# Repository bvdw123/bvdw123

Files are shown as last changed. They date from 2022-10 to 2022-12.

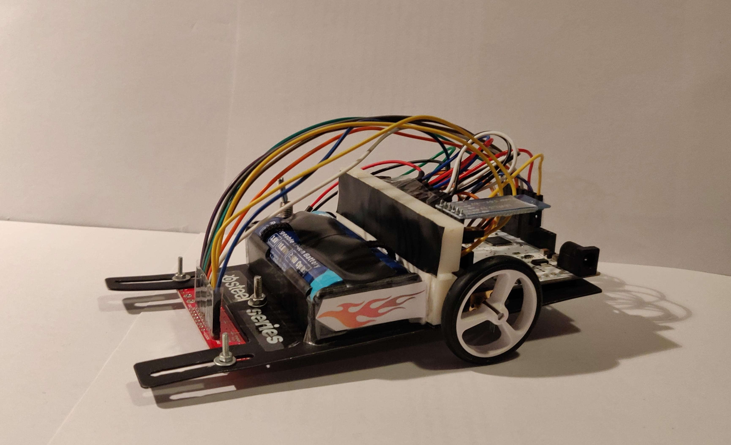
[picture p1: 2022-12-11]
technische tekeningen/mechanisch/LineFollower.jpg

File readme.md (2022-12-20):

# LineFollower
<br />
<br />
<br />
LineFollower

<br />
<br />
  
## specifications
<br />
microcontroller: Arduino Leonardo
<br />
motors: Micro Metal Gearmotor 50:1 
<br />
h-bridge: DRV8833
<br />
sensors: QTR-8A
<br />
batteries: XTAR 18650 Li-Ion
<br />
wireless communication: HC-05
<br />
distance sensor - motors: 85 mm
<br />
weight: 240 g
<br />
speed: 0,431 m/s
<br />

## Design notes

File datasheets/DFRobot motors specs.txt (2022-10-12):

 Specification 50:1

    Motor speed (No gearbox):13000 rpm
    Gear ratio: 50:1 
    Motor speed (with gearbox): 400rpm±10%
    Rated current: 55mA @ 6V
    Stall current: 350mA @ 6V
    Stall torque: 0.39kg*cm @ 6V

 Specification 30:1

    Working voltage: 3 or 6 volts
    15000 rpm @6v No load
    30:1 Gear ratio
    700rpm±10% @6V With load
    No-load Current: 55mA @ 6V
    700mA stall current @ 6V
    Torque:1.2Kg/cm @6V

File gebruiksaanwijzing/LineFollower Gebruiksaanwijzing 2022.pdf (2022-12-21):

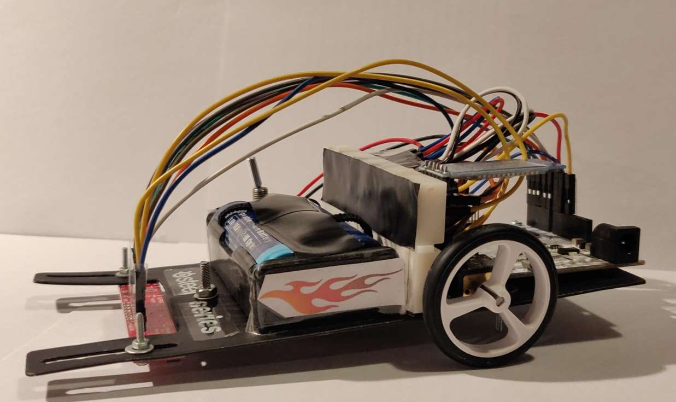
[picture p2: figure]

1
Handleiding $teelseries Ultra Speed Max Performance LineFollower

# Gebruiksaanwijzing $teelseries Ultra Speed Max Performance LineFollower

Benjamin Vande Walle | 3 EM-AM 2022

In dit document wordt beschreven hoe de $teelseries Ultra Speed Max Performance LineFollower veilig te gebruiken.

2

## Inhoud

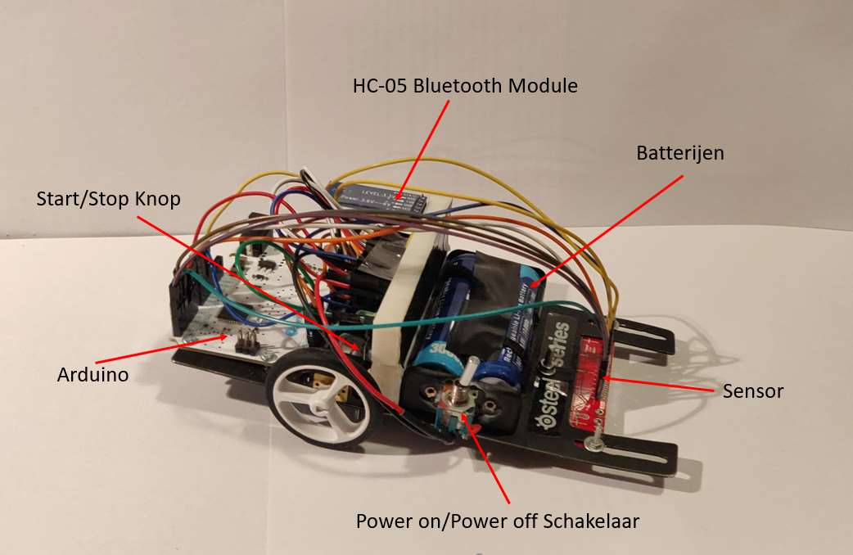
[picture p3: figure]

3

## 1 Algemene waarschuwing

Vrijwaring: bevat kleine onderdelen die een mogelijks verstikkingsgevaar vormen, niet geschikt voor kinderen onder 12 jaar, altijd onder ouderlijk toezicht gebruiken.
Bij verkeerd gebruik van de $teelseries Ultra Speed Max Performance LineFollower gevaar op rook-en vuurontwikkeling. De ontwerper van de $teelseries Ultra Speed Max Performance LineFollower is niet verantwoordelijk voor enige vorm van schade zowel lichamelijk als materieel.

## 2 Overzicht LineFollower

Figuur 1: overzicht van de verschillende componenten LineFollower

4

## 3 Handleiding

### 3.1 Controle voor opstarten

Controleer voor gebruik de robot altijd op mogelijke defecten. Dit kan zijn, maar beperkt zich niet tot:
Losse kabels, vervorming van één of beide batterijen, wielen niet stevig verbonden, moeren niet goed aangespannen of losgekomen door trillingen bij vorig gebruik, afwezigheid van decoratieve vlammen, losse componenten …
Visuele inspectie zorgt voor een langere levensduur van de robot en helpt gevaarlijke situaties voorkomen!

### 3.2 Opstarten

Om de $teelseries Ultra Speed Max Performance LineFollower van stroom te voorzien dient men de ON/OFF schakelaar (zie figuur 1) in de ON positie (rood) te plaatsen. De ingebouwde led op de Arduino en de power led op de robot gaan aan. Als de indicatie led’s niet branden na het inschakelen van de robot zie “Troubleshooting”.

### 3.3 Bluetooth verbinding

Wanneer de robot opgestart is, kan men verbinding met de robot maken via bluetooth. Wanneer de rode en blauwe led op de bluetooth module om de halve seconde knipperen is ook de module correct opgestart en klaar om te verbinden.
Schakel bluetooth op uw computer aan¹
en verbind met de robot.
Naam van de module: HC-05_B
Wachtwoord: 1234
Typ in de zoekbalk apparaat beheer en ga naar poorten. Normaal staan er twee poorten met bluetooth: standaard seriële verbinding via Bluetooth (COMx), de onderste poort is degene waarmee verbonden moet worden.
Start het programma Arduino IDE op door Arduino in de zoekbalk te typen en verbind met de robot: Arduino bord: Leonardo
COM-poort: COMx (onderste lijn bij apparaat beheer)
Wanneer de led’s van de module om de twee seconden knipperen is de computer met de module verbonden.
De robot is nu succesvol met de computer verbonden, deze kan nu commando’s ontvangen en informatie terugsturen.
1: Zie “Pair a Bluetooth device in Windows” of “Connect a Bluetooth device with your Mac”.

### 3.4 Kalibreren

Voor gebruik is het nodig om de sensor te kalibreren zodanig dat de sensor optimaal werkt. De sensor moet voor zowel witte als zwarte oppervlakken gekalibreerd worden.
Plaats de robot op een wit oppervlak dat gebruikt wordt op het parcours, typ via de seriële monitor het commando “calibrate white” in en wacht tot er “done” op de monitor komt.

5

Plaats de robot op een zwart oppervlak dat gebruikt wordt op het parcours, typ via de seriële monitor het commando “calibrate black” in en wacht tot er “done” op de monitor komt.
Zie Commando’s voor meer informatie.

### 3.5 Starten en stoppen van de robot via Bluetooth

Nu de robot stroom krijgt, verbonden is met de seriële monitor en kalibratie voltooid is, kan de robot gestart worden. Plaats de robot op het parcours met de sensor boven de zwarte lijn. Typ het commando “start” in. Om de robot te stoppen wordt het commando “stop” gebruikt.
Wanneer de robot van het parcours gaat of de zwart lijn niet meer detecteert zal de robot automatisch stoppen. Om de robot opnieuw te kunnen starten, moet het commando “start” opnieuw ingevoerd worden. Schakel de robot na gebruik altijd uit door de power schakelaar op de off positie (zwart) te plaatsen.
Zie Commando’s voor meer informatie.

6

## 4 Gebruik

### 4.1 Commando’s

De verschillende commando’s om de robot te sturen, typ het commando in de seriële monitor en druk op enter.

### 1 Commando: “start”

Hiermee zal de robot starten en blijven rijden zolang er een zwart lijn gedetecteerd wordt.

### 2 Commando: “stop”

Dit stopt de robot.

### 3 Commando: “debug”

Het commando om de verschillende parameters van de robot weer te geven.

### 4 Commando: “diff”

Hiermee kan de parameter diff ingesteld worden. Als de robot versneld in de bochten moet deze verlaagd worden (0 – 1), als de robot vertraagd of stopt in de bochten moet deze verhoogd worden.

### 5 Commando: “set cycle x”

Hiermee kan de cyclus tijd van het programma ingesteld worden. In microseconden (het dubbele van de calculation time (zie debug)).

### 6 Commando: “calibrate white”

Om de sensor de kleur wit te laten kalibreren, plaats je de sensor over het witte oppervlakte en voer je het commando in.

### 7 Commando: “calibrate black”

Om de sensor de kleur zwart te laten kalibreren, plaats je de sensor over het zwarte oppervlakte en voer je het commando in.

### 8 Commando: “set power x”

Hiermee kan de snelheid van de robot ingesteld worden (0 – 255).
PID instellen (voor gevorderde gebruikers)

### 9 Commando: “set kp x”

Hiermee kan de proportionele parameter ingesteld worden(0 – 20).
- stuurt de robot niet snel genoeg bij => verhoog Kp
- waggelt de robot over de zwarte lijn => verlaag Kp

### 10 Commando: “set ki x”

Hiermee kan de integrerende parameter ingesteld worden (0 – 1).

### 11 Commando: “set kd x”

Hiermee kan de differentiërende parameter ingesteld worden (0 – 1).

7

8

### 4.2 Starten met knop

Om de robot te starten zonder Bluetooth connectie kan men gebruik maken van de knop. Door één keer op de knop te drukken zal de robot starten. Wanneer men opnieuw de knop indrukt zal de robot stoppen, daarna kan me de robot opnieuw starten door op de knop te duwen. Zonder tussenkomst zal de robot enkel stoppen wanneer deze geen zwarte meer lijn detecteert.

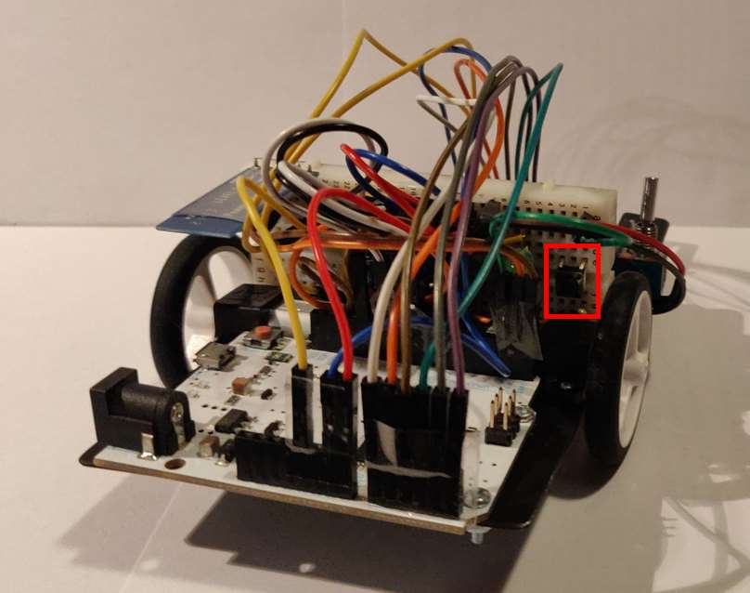
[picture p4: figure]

Figuur 2: start/stop knop

### 4.3 Batterijen

Om de batterijen op te laden moeten deze uit de batterijhouder gehaald worden en in een daar voorziene Li-Ion oplader geplaatst worden. Bij het plaatsen van de batterijen moet altijd op de polariteit gelet worden. Gebruik altijd de correcte lader voor Li-Ion batterijen.

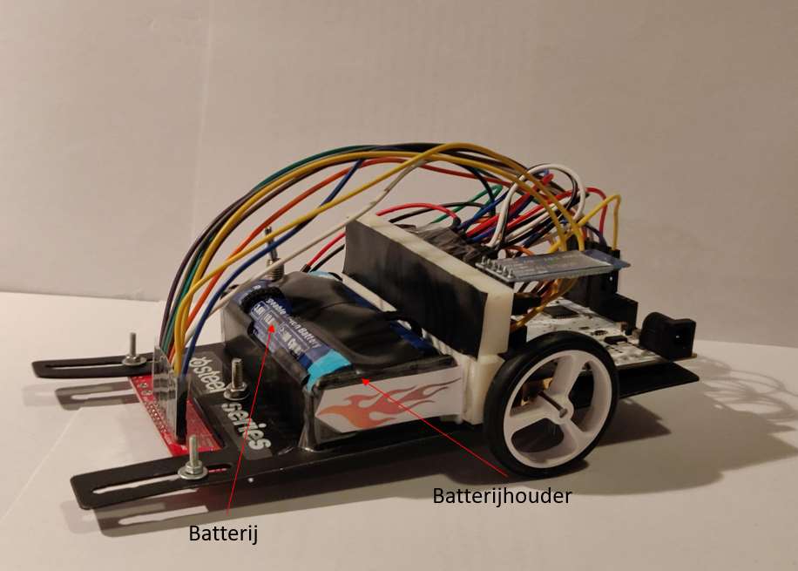
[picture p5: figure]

Figuur 3: Duiding batterijen en houder

9

10

## 5 Troubleshooting

1 | Probleem | Oorzaak | Oplossing
2 | Indicator led’s branden niet | On/Off schakelaar niet op “on” positie | Schakelaar naar “on” positie verplaatsen
3 Batterijen niet | | opgeladen | Batterijen opladen
4 | | Andere fout | Contact opnemen met producent
5 | Kan niet verbinden met bluetooth | Bluetooth niet ingeschakeld | Bluetooth inschakelen
6 Verkeerd wachtwoord | | ingegeven | Correct wachtwoord ingeven
7 Bluetooth module niet | | opgestart | Module opstarten door power schakelaar naar “on” positie te verplaatsen
8 Bluetooth module niet | | aanwezig op robot of verloren tijdens gebruik | Contact opnemen met producent
9 Geen verbinding met | | computer
10 Indicatie led’s blijven | | om de halve seconde knipperen | Robot opnieuw opstarten
11 Robot heeft niet alleen decoratieve | vlammen | Vuur | Stop commando invoeren, blussen en/of brandweer bellen
12 | Robot reageert niet op commando’s | Geen Bluetooth connectie/ connectie verloren | Bluetooth connecteren

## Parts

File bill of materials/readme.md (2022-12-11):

## bill of materials
<br />

|volgnummer |naam |omschrijving |nieuw/recup|kostprijs/stuk|aantal|subtotaal|
|--- |---- |--- |---|---|---|---|
| 1|QTR-8A |Reflectiesensor |Nieuw | 10,95| 1| 10,95|
| 2|HC-05 |Bluetooth module |Nieuw | 6,5| 1| 6,5|
| 3|Micro Metal Gearmotor Bracket Pair |Motorsteurn/houder |Nieuw | 4,7| 1| 4,7|
| 4|Pololu Wiel |Wiel 40×7mm |Nieuw | 4,9| 1| 4,9|
| 5|XTAR 18650 |Li-Ion batterij 3000mAh (protected) - 4.5A |Nieuw | 8,95| 2| 17,9|
| 6|18650 Batterijhouder |Batterijhouder voor type 18650 |Nieuw | 1,75| 1| 1,75|
| 7|Micro Metal Gearmotor |Motor verhouding 50:1 650 rpm |Nieuw | 5,87| 2| 11,75|
| 8|Chassis |Aluminium plaat |Recup | 0| 1| 0|
| 9|Dupont kabels |Kabels |Recup | 0| /| 0|
| 10|Breadbord |Breadbord |Recup | 0| 1| 0|
| 11|Velcro |Velcro |Nieuw |  2 euro/meter| 1| 2|
| 12|Microcontroller |Arduino Leonardo |Recup | 0| 1| 0|
| 13|DRV8833 |H-brug |Nieuw | 6,5| 1| 6,5|
| 14|Push button |Drukknop |Recup | 0| 1| 0|
| 15|Bouten/moeren |Bouten/moeren |Recup | 0| 12| 0|
| 16| | | | |TOTAAL| 66,95|

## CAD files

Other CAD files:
technische tekeningen/mechanisch/Chassis-1_2D.dwg

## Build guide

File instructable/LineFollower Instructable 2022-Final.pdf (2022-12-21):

# Instructable LineFollower


## Inhoudstafel

## 1 Doel:


Figuur 1: Overzicht LineFollower

## 2 Voorbereiding en info

Link naar de GitHub pagina:
https://github.com/bvdw123/bvdw123
Link naar de handleiding (bij voltooien van deze instructable): https://github.com/bvdw123/bvdw123/blob/main/gebruiksaanwijzing/LineFollower%20Gebruiksaa nwijzing%202022.pdf

## 3 Bouwen van de LineFollower

### Stap 1: Componenten bestellen

Bestel de componenten beschreven in de Bill Of Materials.

Nr | Naam | Omschrijving | Recup | Prijs/Stuk | Aantal | Subtotaal
1 | QTR-8A | Reflectiesensor | Nee | 10,95 | 1 | 10,95
2 | HC-05 | Bluetooth module | Nee | 6,5 | 1 | 6,5
3 | Bracket Pair | Motorsteurn/houder | Nee | 4,7 | 1 | 4,7
4 | Pololu Wiel | Wiel 40×7mm | Nee | 4,9 | 1 | 4,9
5 | XTAR 18650 | Li-Ion batterij 3000mAh | Nee | 8,95 | 2 | 17,9
6 | 18650 Batterijhouder | Batterijhouder type 18650 | Nee | 1,75 | 1 | 1,75
7 | Gearmotor | Motor 50:1 650 rpm | Nee | 5,87 | 2 | 11,75
8 | Chassis | Aluminium plaat | Ja | 0 | 1 | 0
9 | Dupont kabels | Kabels | Ja | 0 | 1 | 0
10 | Breadbord | Breadbord | Ja | 0 | 1 | 0
11 | Microcontroller | Arduino Leonardo | Ja | 0 | 1 | 0
12 | DRV8833 | H-brug | Nee | 6,5 | 1 | 6,5
13 | Push button | Drukknop | Ja | 0 | 1 | 0
14 | Schakelaar | Schakelaar | Ja | 0 | 1 | 0
15 | Bouten/moeren | Bouten/moeren | Ja | 0 | 12 | 0
| | | | | TOTAAL | 66,95
https://github.com/bvdw123/bvdw123/tree/main/bill%20of%20materials

### Stap 2: Chassis maken

Maak de gaten en openingen in de aluminium plaat volgens de technische tekening in bijlage één.

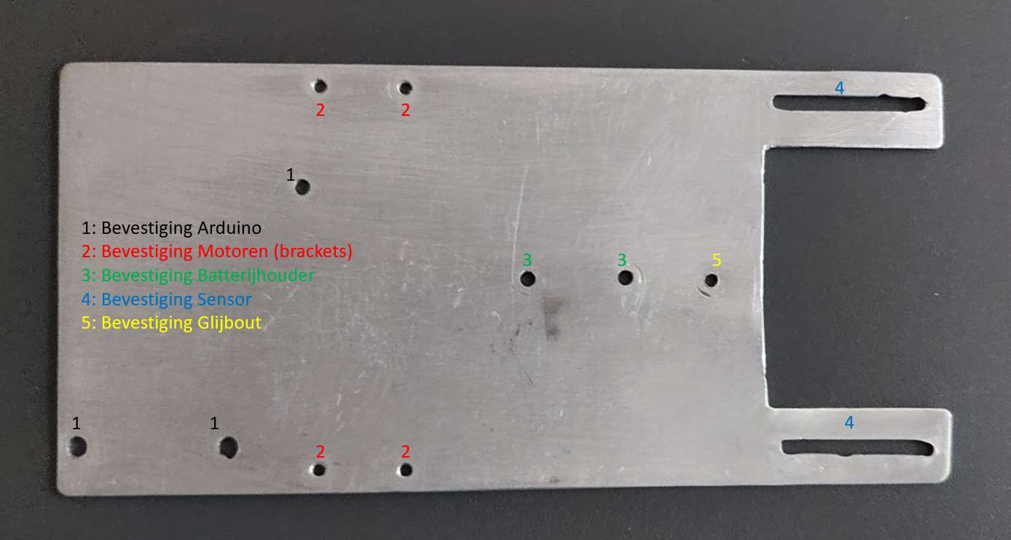
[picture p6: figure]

Figuur 2: Layout chassis

### Stap 3: Arduino programmeren

Download het programma op de GitHub pagina. Verbind de Arduino Leonardo met de computer en laad het programma via de Arduino IDE in de microcontroller.

### Stap 4: Arduino monteren

Plaats de Arduino op het chassis aan de achterkant zodanig dat de boringen van de Arduino overeenkomen met de gaten (zie figuur Layout chassis: 1) in het chassis. Plaats de M2 bouten in de boringen en span de moeren aan zodat de Arduino vastzit maar niet te hard om schade te voorkomen.

### Stap 5: Motoren monteren

Plaats de motoren in de brackets. Plaats de brackets met motoren op het chassis. Zorg dat de voorziene gaten in de brackets overeenkomen met de boringen (zie figuur Layout chassis: 2) in het chassis. Plaats de M2 bouten in de gaten en span stevig aan.

### Stap 6: Schakelaar en breadbord aan batterijhouder monteren

Verbind de kabel van de batterijhouder met de schakelaar. Breng lijm aan de (korte) zijkant van de schakelaar en de batterijhouder en maak deze vast. Breng lijm of dubbelzijdige plakband aan de onderkant van het breadbord aan en verbind met de (lange) zijkant van de batterijhouder. Plaats de H-brug en knop op het breadbord.

### Stap 7: Batterijhouder met breadbord monteren

Plaats de batterijhouder met het breadbord naar de Arduino gericht op het chassis zodat de boringen in het chassis overeenkomen met de boringen (zie figuur Layout chassis: 3) op het chassis. Verbind met de M2 bouten en span stevig aan.

### Stap 8: Sensor monteren

Plaats de sensor onder het chassis zodat de boringen in de sensor overeenkomen met de gleuven (zie figuur Layout chassis: 4) van het chassis. De sensoren (zwarte blokjes op sensor) moeten naar de grond gericht zijn. Plaats de M2 bouten met bijhorende sluitring. De gleuven zijn er om de afstand tussen sensor en wielbasis te kunnen regelen.

### Stap 9: Elektronica opbouwen

Verbind de componenten volgens het elektrisch schema in bijlage twee. Pinouts:
Component pin | Arduino pin
HC-05
GND | GND
VCC | 5V
RX | TX
TX | RX

Sensor
GND | GND
VCC | 5V
S1 | A0
S2 | A1
S3 | A2
S4 | A3
S5 | A4
S6 | A5

H-Brug
GND | GND
VCC | 5V
Vm | Batterij 9V
SLP | 5V
A1IN | D13 (PWM)
A2IN | D11 (PWM)
B1IN | D10 (PWM)
B2IN | D9 (PWM)
A1OUT | Motor M1 1
A2OUT | Motor M1 2
B1OUT | Motor M2 1
B2OUT | Motor M2 2

### Stap 10: wielen op motoren monteren

Breng de band aan op het wiel. De assen van de motoren en de gaten van de wielen hebben een D vorm. Plaats de wielen op de assen zodat de vorm van de as gelijk loopt met de vorm van het asgat in het wiel. Schuif de wielen op de as.

### Stap 11: Glijbout monteren

Neem een bout M3 en plaats deze in de correcte boring (zie figuur Layout chassis: 5). Plaats de bout zodat deze met de kop de grond raakt. Maak de bout vast zodanig dat de optimale afstand van sensor tot blad van 3mm bereikt is.

### Stap 12: Batterijen plaatsen

Plaats de batterijen volgens de juiste polariteit in de batterijhouder. Laad Li-Ion batterijen altijd met de correcte lader op.

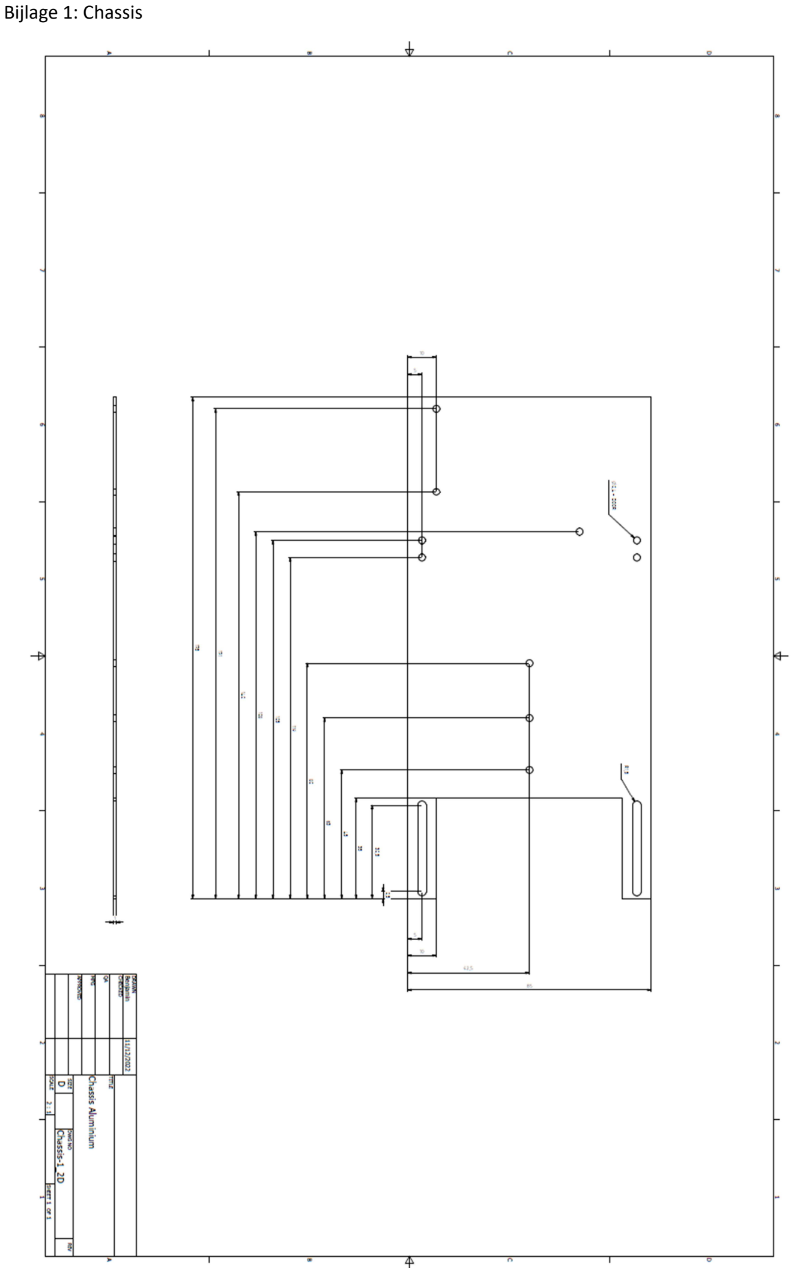
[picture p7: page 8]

Bijlage 1: Chassis

Bijlage 2: Elektrisch schema

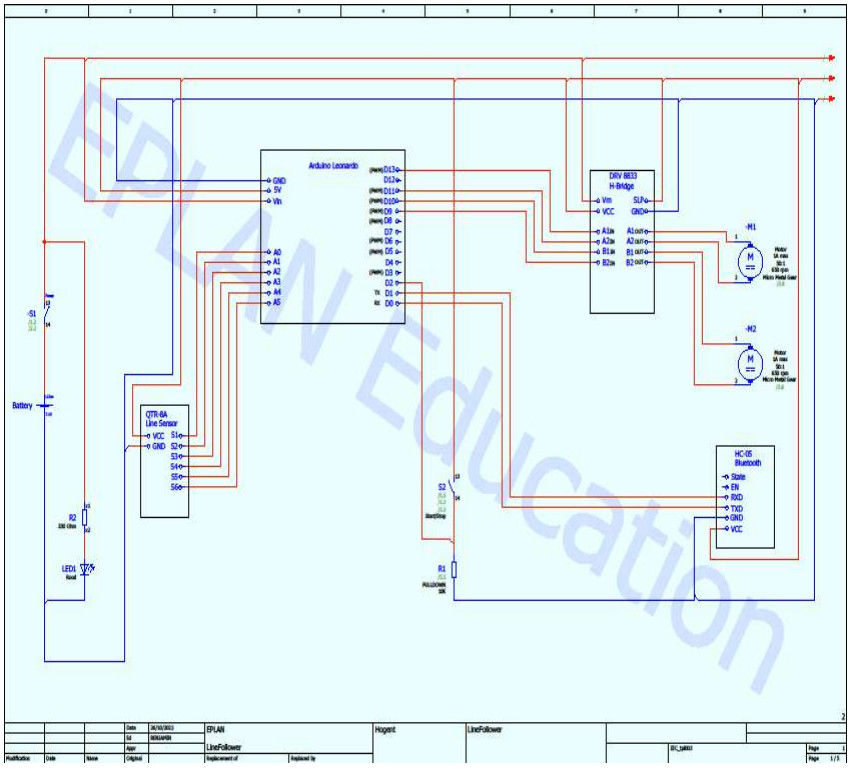
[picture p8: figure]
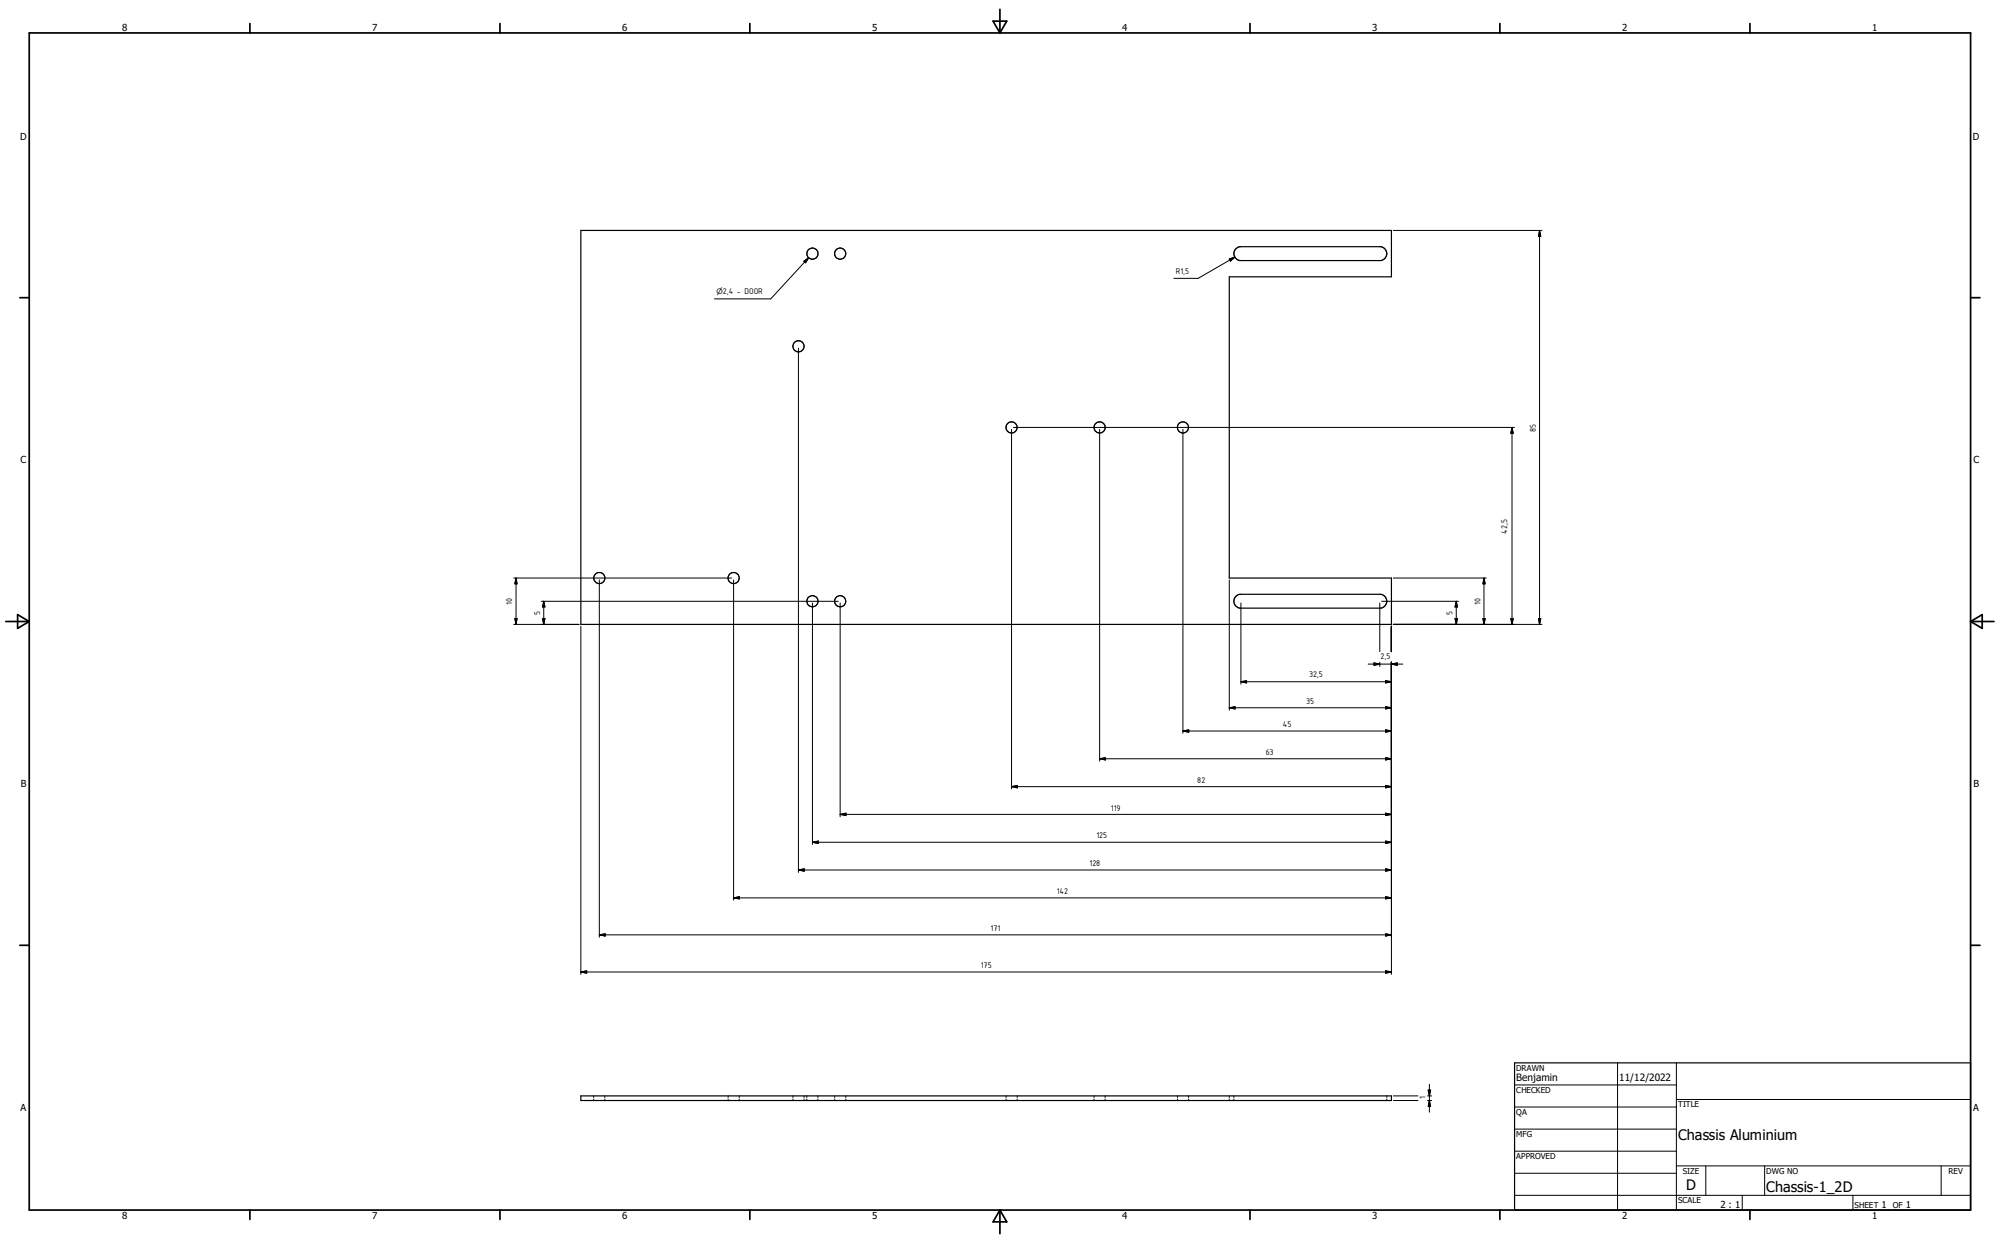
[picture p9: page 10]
TITLE; Chassis Aluminium; n2,4 - DOOR

DRAWN Benjamin | 11/12/2022

CHECKED

MFG

APPROVED

SIZE D | | DWG NO Chassis-1_2D | REV

SCALE | | SHEET 1 OF 1

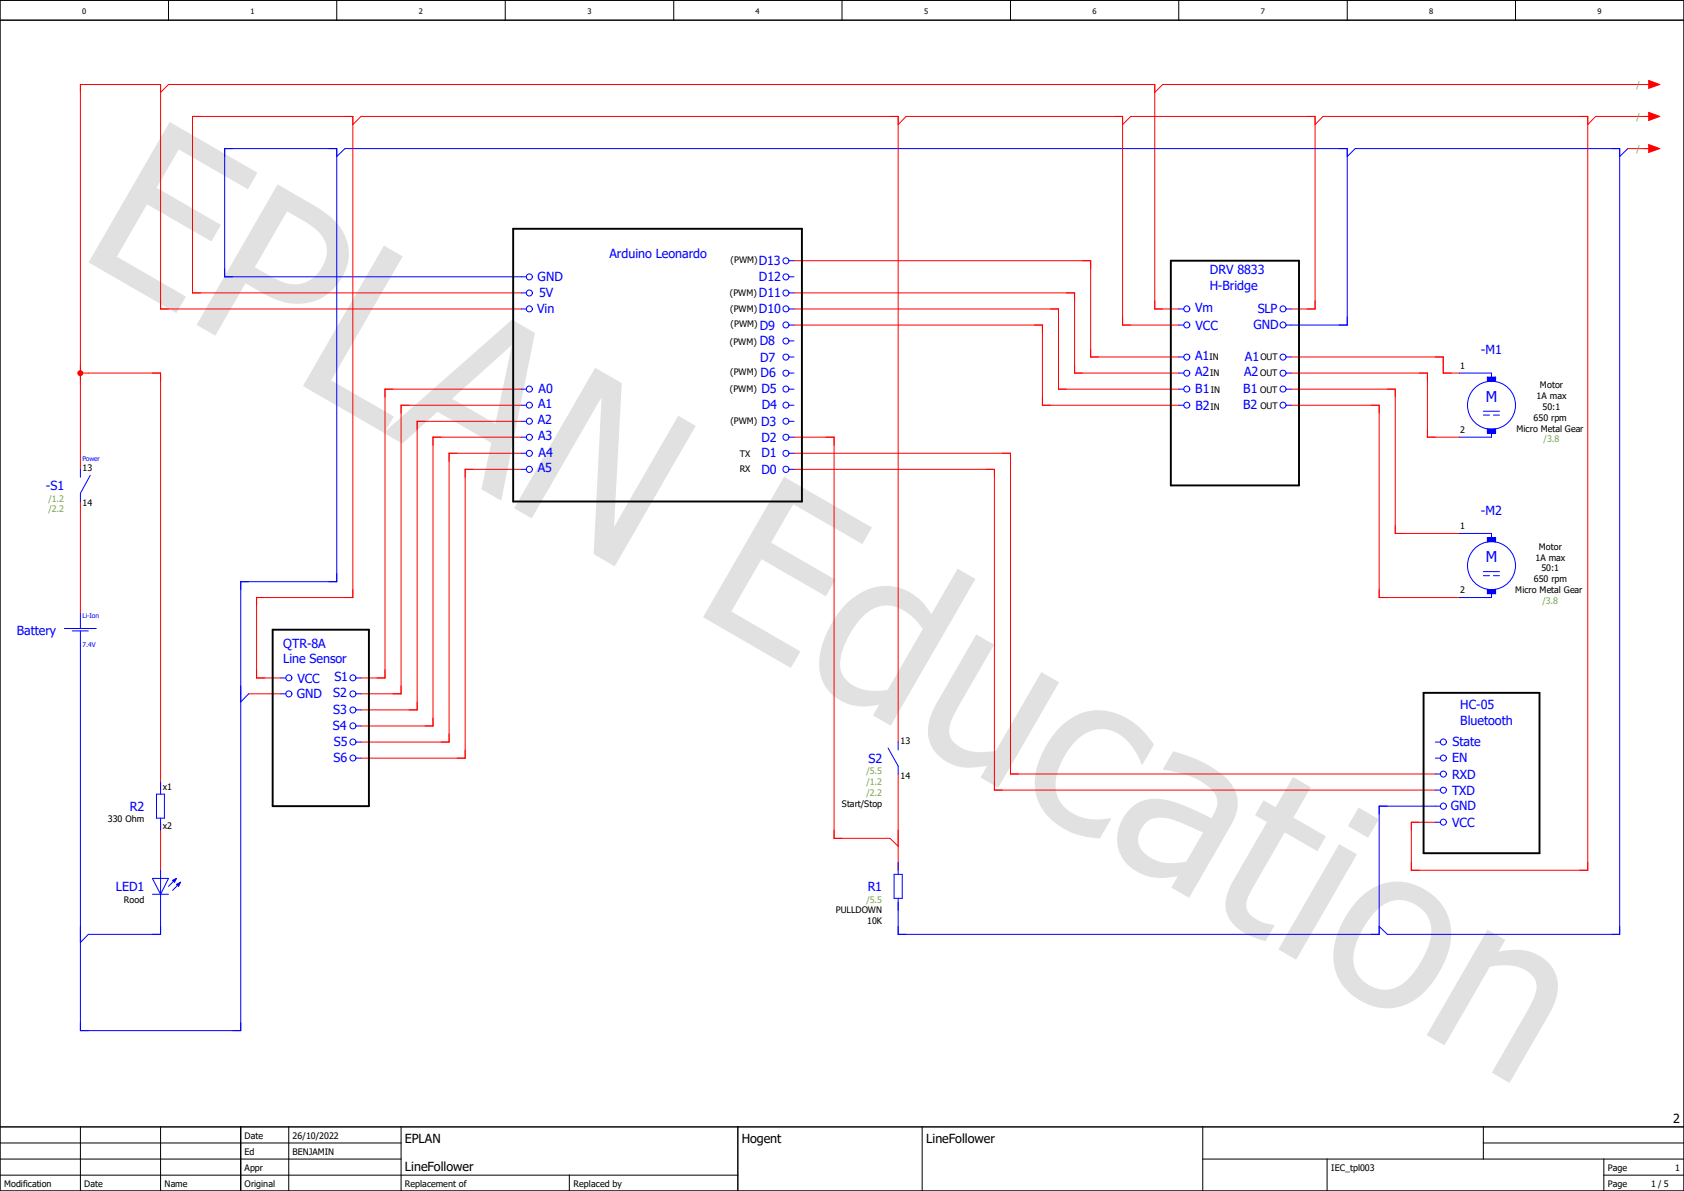
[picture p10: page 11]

Ed | BENJAMIN
Appr

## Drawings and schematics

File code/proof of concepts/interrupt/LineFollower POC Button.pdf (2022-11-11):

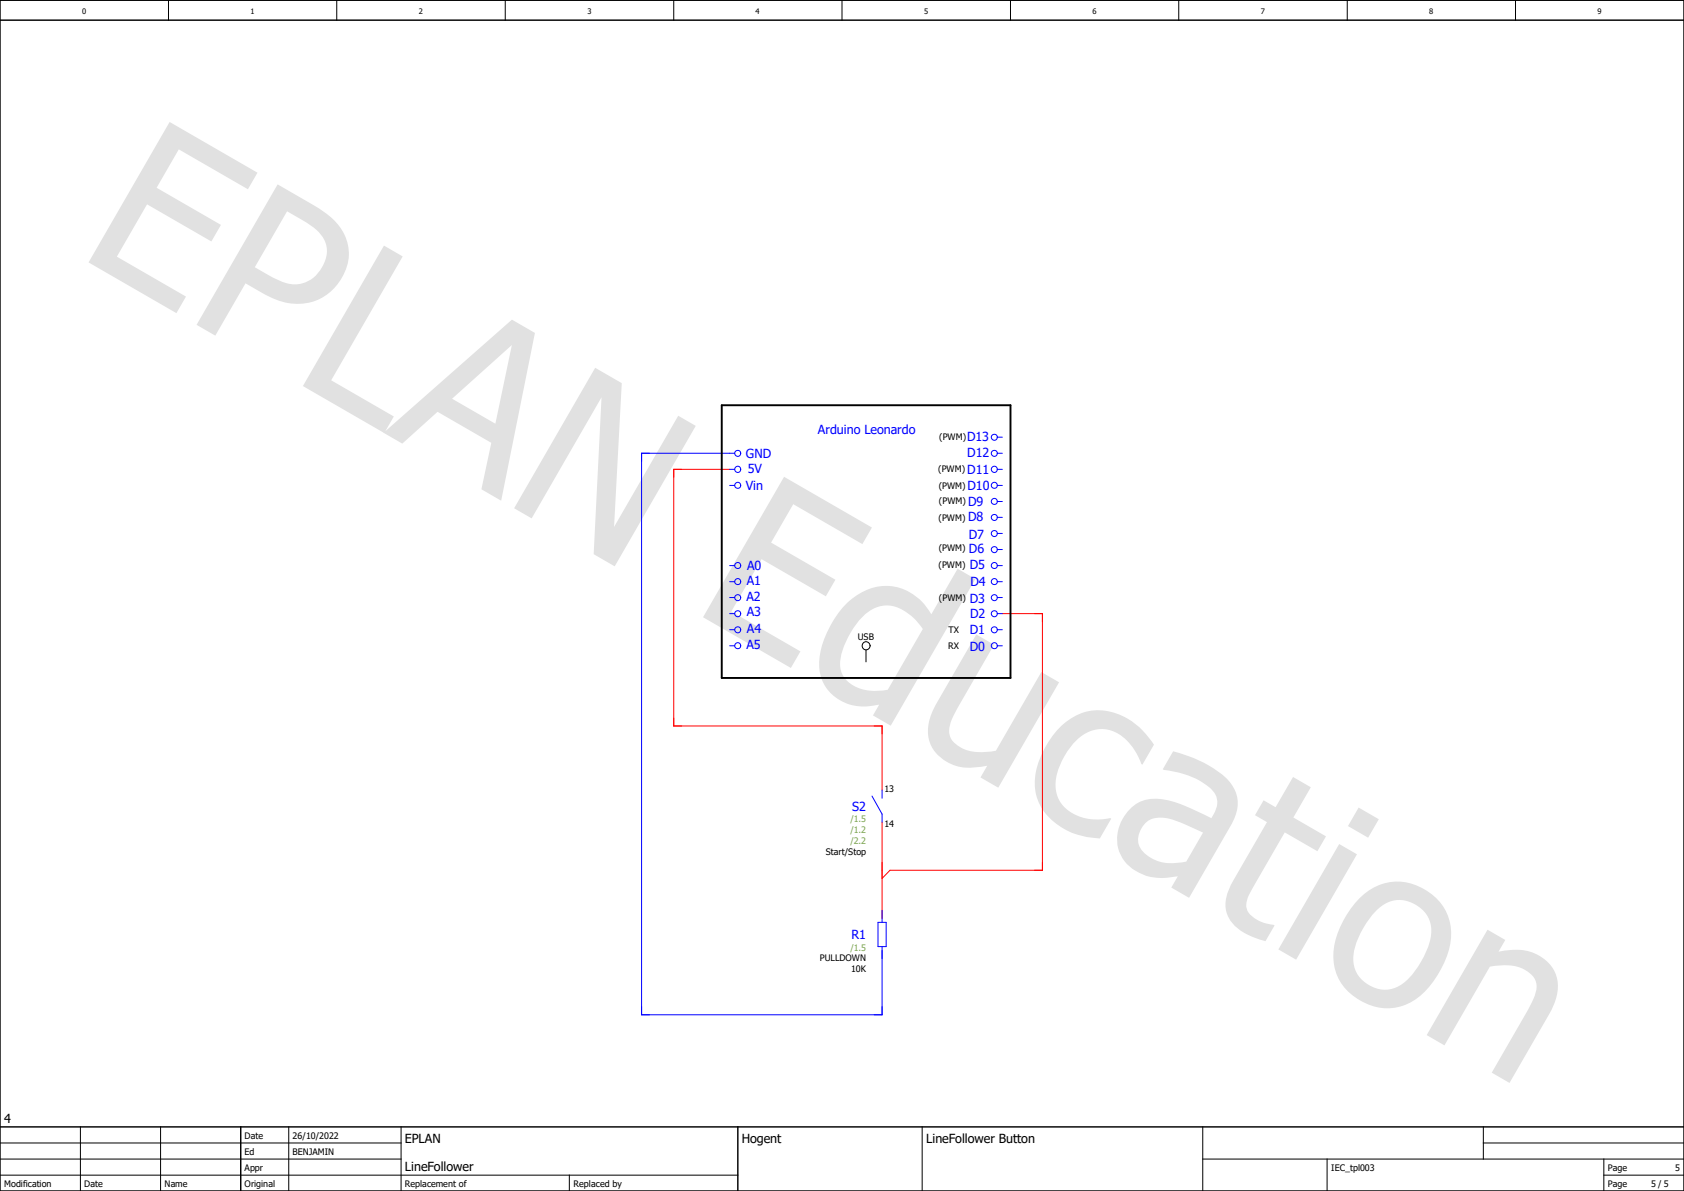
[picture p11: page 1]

Date | 26/10/2022 | EPLAN LineFollower | Hogent | LineFollower Button
Ed | BENJAMIN
Appr | | | | | IEC_tpl003 | Page 5

Modification | Date | Name | Original | | Replacement of | Replaced by | | | | Page 5 / 5

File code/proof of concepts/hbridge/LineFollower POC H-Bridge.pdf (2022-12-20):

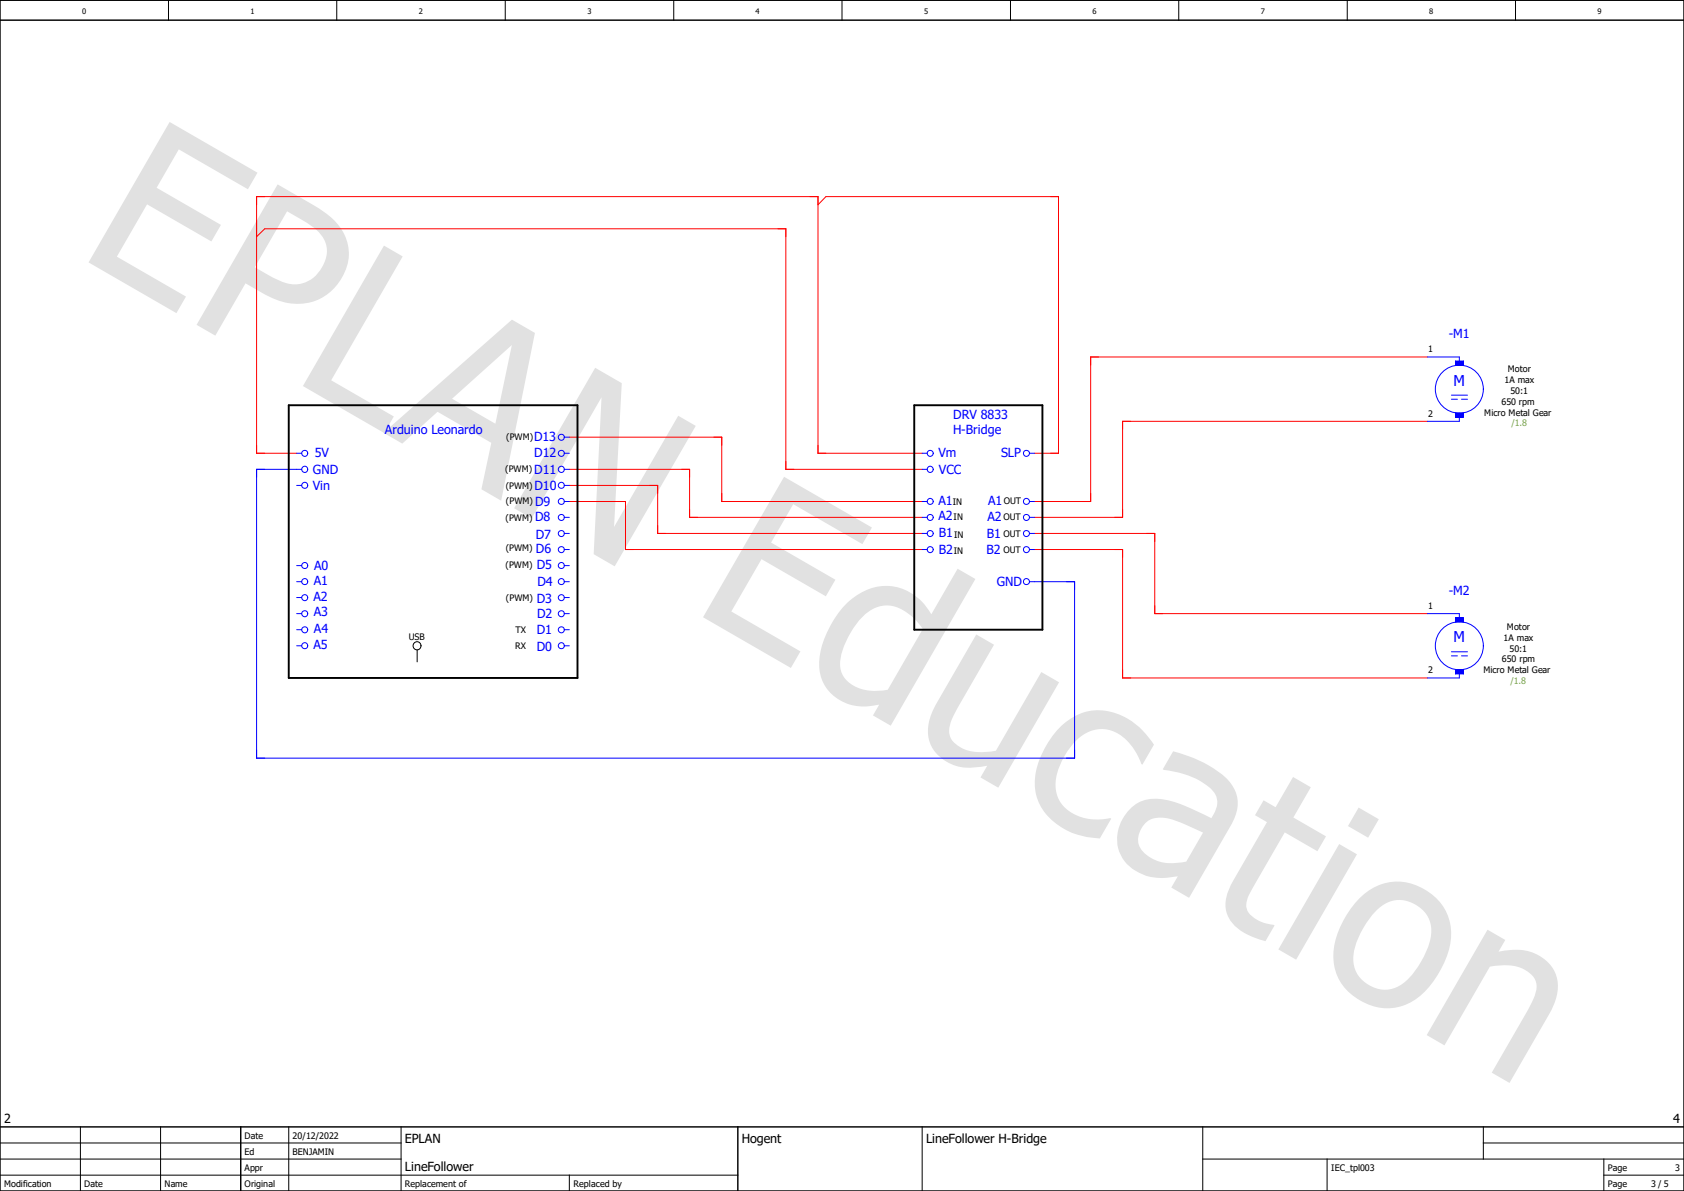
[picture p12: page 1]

Date | 20/12/2022 | EPLAN LineFollower | Hogent | LineFollower H-Bridge
Ed | BENJAMIN
Appr | | | | | IEC_tpl003 | Page 3

Modification | Date | Name | Original | | Replacement of | Replaced by | | | | Page 3 / 5

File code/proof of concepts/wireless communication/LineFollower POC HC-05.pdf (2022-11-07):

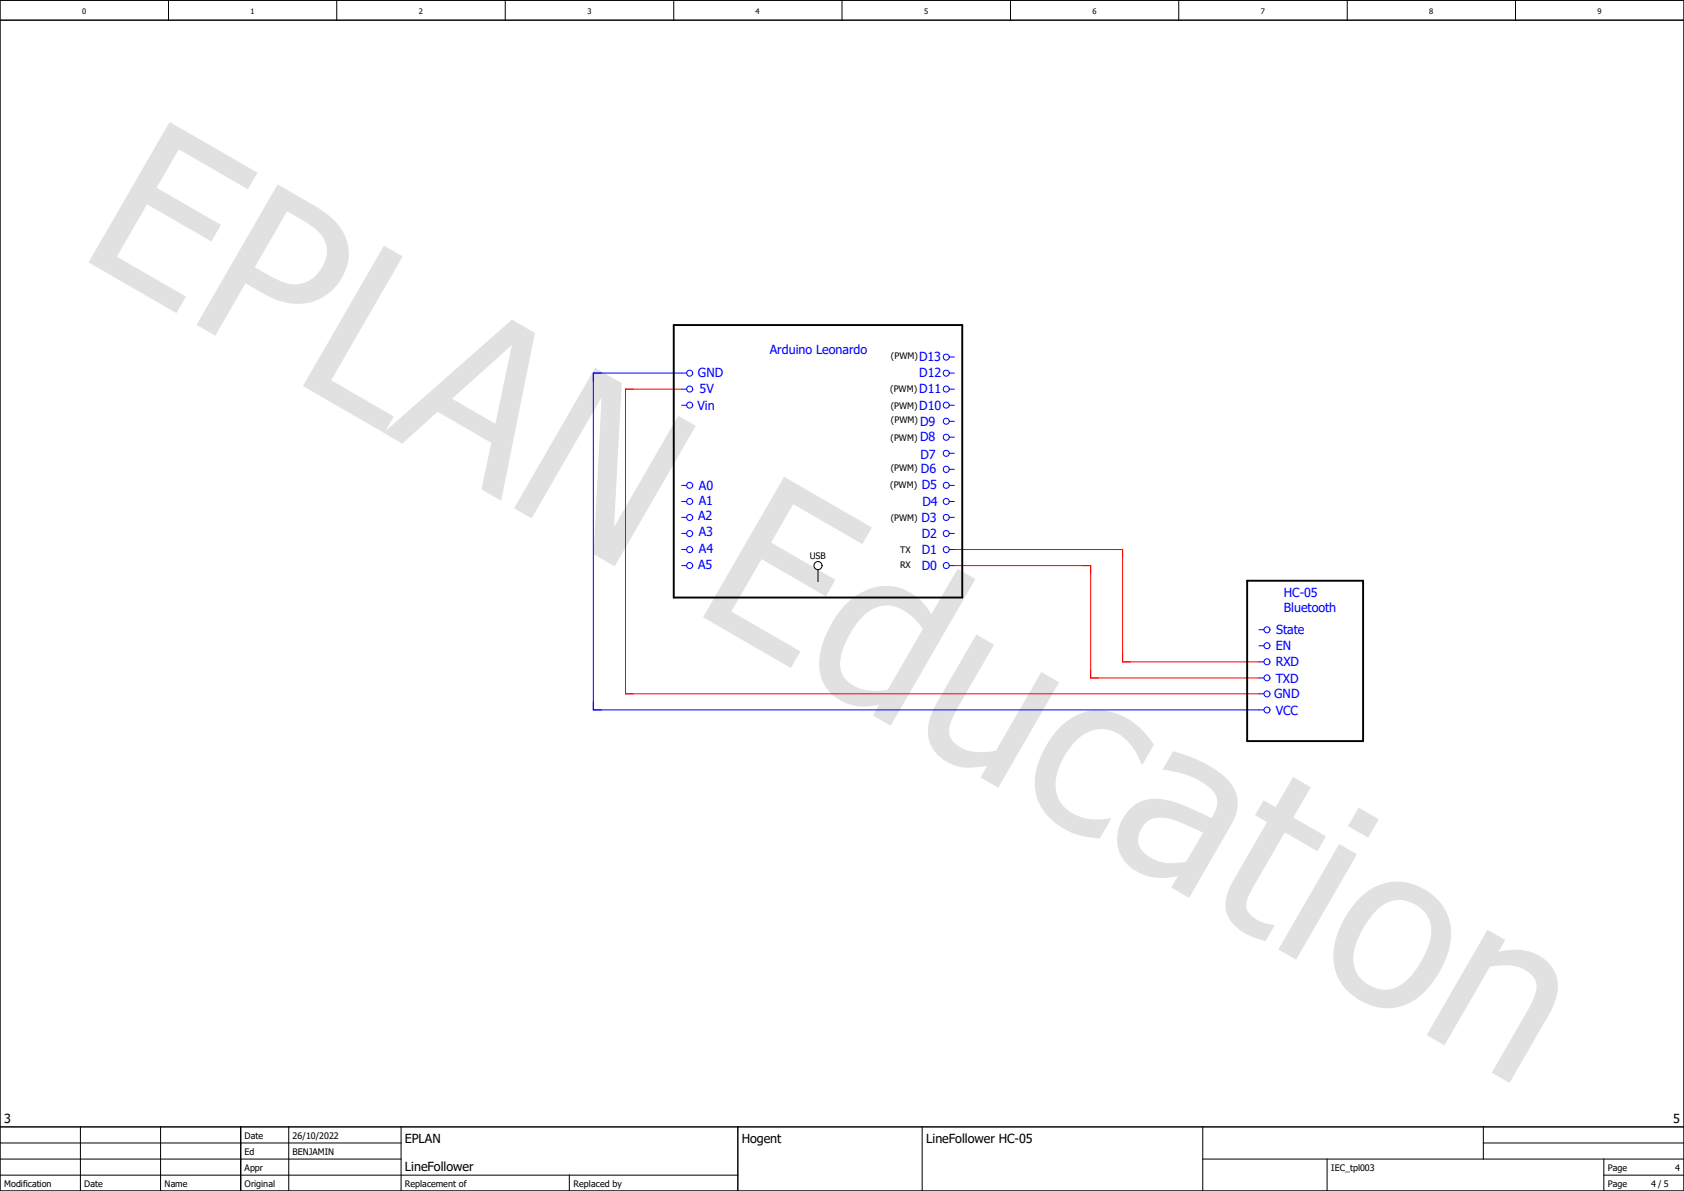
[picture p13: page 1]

Date | 26/10/2022 | EPLAN LineFollower | Hogent | LineFollower HC-05
Ed | BENJAMIN
Appr | | | | | IEC_tpl003 | Page 4

Modification | Date | Name | Original | | Replacement of | Replaced by | | | | Page 4 / 5

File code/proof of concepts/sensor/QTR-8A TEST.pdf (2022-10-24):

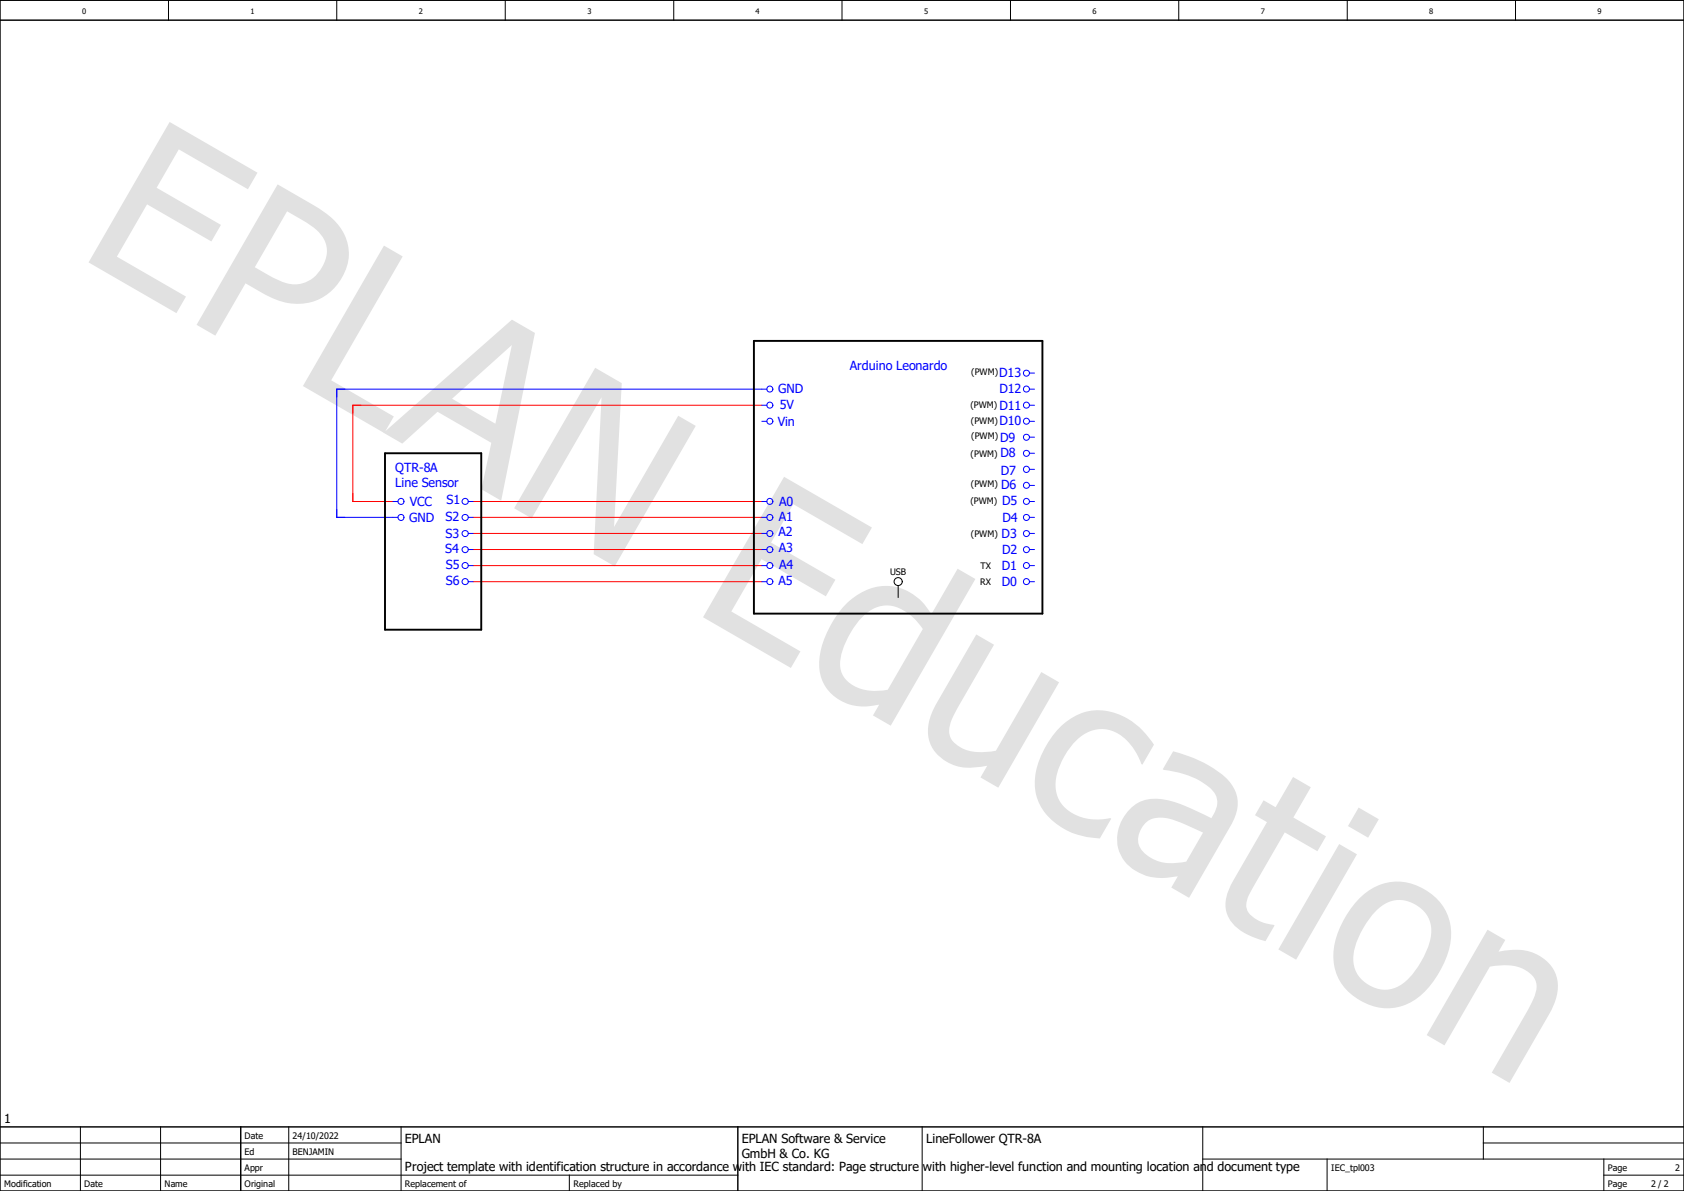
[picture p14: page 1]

Date | 24/10/2022 | EPLAN | EPLAN Software & Service GmbH & Co. KG | LineFollower QTR-8A
Ed | BENJAMIN
Appr | | | | | IEC_tpl003 | Page 2

Project template with identification structure in accordance with IEC standard: Page structure with higher-level function and mounting location and document type

Modification | Date | Name | Original | | Replacement of | Replaced by | | | | Page 2 / 2

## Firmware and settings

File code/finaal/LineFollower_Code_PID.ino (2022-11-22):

// Empty met kalibratie toegevoegd 17/11/2022

#include "SerialCommand.h"
#include "EEPROMAnything.h"

#define SerialPort Serial1
#define Baudrate 115200

#define AIN1 13
#define AIN2 11
#define BIN1 10
#define BIN2 9

#define interruptPin 2

SerialCommand sCmd(SerialPort);
bool debug;

unsigned long previous, calculationTime;


const int sensor[] = {A0, A1, A2, A3, A4, A5};

long normalised[6];
float debugPosition;
float iTerm;

struct param_t
{
  /* andere parameters die in het eeprom geheugen moeten opgeslagen worden voeg je hier toe ... */
  unsigned long cycleTime;
  int black[6];
  int white[6];
  uint16_t power;
  float diff;
  float kp;
  float ki;
  float kd;
  bool run;

} params;


void setup()
{
  SerialPort.begin(Baudrate);

  sCmd.addCommand("stop", onStop);
  sCmd.addCommand("start", onStart);
  sCmd.addCommand("calibrate", onCalibrate);
  sCmd.addCommand("set", onSet);
  sCmd.addCommand("debug", onDebug);
  sCmd.setDefaultHandler(onUnknownCommand);

  EEPROM_readAnything(0, params);

  pinMode(interruptPin, INPUT_PULLUP);
  attachInterrupt(digitalPinToInterrupt(interruptPin), button, RISING);

  pinMode(AIN1, OUTPUT);
  pinMode(AIN2, OUTPUT);
  pinMode(BIN1, OUTPUT);
  pinMode(BIN2, OUTPUT);

  params.run = false;

  SerialPort.println("ready");
}

void loop()
{
  sCmd.readSerial();
 
  unsigned long current = micros();
  if (current - previous >= params.cycleTime)
  {
    previous = current;

    /* code die cyclisch moet uitgevoerd worden programmeer je hier ... */

    



    /* normaliseren en interpoleren sensor */

    for (int i = 0; i < 6; i++)
    {
      
      normalised[i]= map(analogRead(sensor[i]),params.black[i], params.white[i], 0, 1000);
      //SerialPort.print(normalised[i]);
      //SerialPort.print(" ");
    }
    //SerialPort.println();

    //Meest zwarte waarde bepalen
    float position;
    int index = 0;
    for (int i = 1; i < 6; i++) if (normalised[i] < normalised[index]) index = i;
    
    //als er geen lijn meer is stoppen
    if (normalised[index] > 950) {

      params.run = false;
      //iTerm = 0;
      
    } 

    //Positie bepalen

    if (index == 0) position = -30;

    else if (index == 5) position = 30;

    else {

      int sNul = normalised[index];
      int sMinEen = normalised[index-1];
      int sPlusEen = normalised[index+1];

      float b = sPlusEen - sMinEen;
      b = b / 2;

      float a = sPlusEen - b - sNul;

      position = -b / (2 * a);

      position += index;
      position -= 2.5;

      position *=15;

    }

    debugPosition = position;

    /* pid regeling */

    /* bereken error = setpoint - positie */
    
    float error = -position;

    //proportioneel regelen

    float output = error * params.kp;

    //output = constrain(output, -510, 510); //output begrenzen voor pwm waardes

    /* integrerend regelen */
    iTerm += params.ki*error;
    iTerm = constrain(iTerm, -510, 510);
    output += iTerm;

    /* differentiërend regelen */

    float lastErr;
    output += params.kd * (error - lastErr);
    lastErr = error;

    /* output begrenzen tot wat fysiek mogelijk is */
    output = constrain(output, -510, 510);


    int powerLeft = 0;
    int powerRight = 0;


    if (params.run) if (output >= 0)
    { 
      powerLeft = constrain(params.power + params.diff * output, -255, 255);
      powerRight = constrain(powerLeft - output, -255, 255);
      powerLeft = powerRight + output;
    }

    else
    {   
      powerRight = constrain(params.power - params.diff * output, -255, 255);
      powerLeft = constrain(powerRight + output, -255, 255);
      powerRight = powerLeft - output;
    }

    /* aansturen motoren */

    analogWrite(AIN1, powerLeft > 0 ? powerLeft : 0);
    analogWrite(AIN2, powerLeft < 0 ? -powerLeft : 0);
    analogWrite(BIN1, powerRight > 0 ? powerRight : 0);
    analogWrite(BIN2, powerRight < 0 ? -powerRight : 0);

  }

  unsigned long difference = micros() - current;
  if (difference > calculationTime) calculationTime = difference;
}

void onUnknownCommand(char *command)
{
  SerialPort.print("unknown command: \"");
  SerialPort.print(command);
  SerialPort.println("\"");
}

void onSet()
{
  char* param = sCmd.next();
  char* value = sCmd.next();  
  
  
    if (strcmp(param, "cycle") == 0)
  {
    long newCycleTime = atol(value);
    float ratio = ((float) newCycleTime) / ((float) params.cycleTime);

    params.ki *= ratio;

    params.cycleTime = newCycleTime;
  }
  else if (strcmp(param, "ki") == 0)
  {
    float cycleTimeInSec = ((float) params.cycleTime) / 1000000;
    params.ki = atof(value) * cycleTimeInSec;
  }

  else if (strcmp(param, "kd") == 0)
  {
    float cycleTimeInSec = ((float) params.cycleTime) / 1000000;
    params.kd = atof(value) / cycleTimeInSec;
  }

  else if (strcmp(param, "power") == 0) params.power = atol(value);
  else if (strcmp(param, "diff") == 0) params.diff = atof(value);
  else if (strcmp(param, "kp") == 0) params.kp = atof(value);

  /* parameters een nieuwe waarde geven via het set commando doe je hier ... */
  
  EEPROM_writeAnything(0, params);
}

void onDebug()
{
  SerialPort.print("cycle time: ");
  SerialPort.println(params.cycleTime);
  
  /* parameters weergeven met behulp van het debug commando doe je hier ... */

  

  SerialPort.print("black: ");
  for (int i = 0; i < 6; i++)
  {
    SerialPort.print(params.black[i]);
    SerialPort.print(" ");
  }
  SerialPort.println(" ");

  SerialPort.print("white: ");
  for (int i = 0; i < 6; i++)
  {
    SerialPort.print(params.white[i]);
    SerialPort.print(" ");
  }
  SerialPort.println(" ");

  SerialPort.print("normalised: ");
  for (int i = 0; i < 6; i++) {
    SerialPort.print(normalised[i]);
    SerialPort.print(" ");
  }
  SerialPort.println(" ");

  SerialPort.print("position: ");
  SerialPort.println(debugPosition);

  SerialPort.print("power: ");
  SerialPort.println(params.power);
  SerialPort.print("diff: ");
  SerialPort.println(params.diff);
  SerialPort.print("kp: ");
  SerialPort.println(params.kp);

  float cycleTimeInSec = ((float) params.cycleTime) / 1000000;
  float ki = params.ki / cycleTimeInSec;
  SerialPort.print("Ki: ");
  SerialPort.println(ki);

  float kd = params.kd * cycleTimeInSec;
  SerialPort.print("Kd: ");
  SerialPort.println(kd);

  SerialPort.print("running: ");
  SerialPort.println(params.run);


  
  SerialPort.print("calculation time: ");
  SerialPort.println(calculationTime);
  calculationTime = 0;
}

void onCalibrate()
{
  char* param = sCmd.next();

  if (strcmp(param, "black") == 0)
  {
    SerialPort.print("start calibrating black... ");
    for (int i = 0; i < 6; i++) params.black[i]=analogRead(sensor[i]);
    SerialPort.println("done");
  }
  else if (strcmp(param, "white") == 0)
  {
    SerialPort.print("start calibrating white... ");    
    for (int i = 0; i < 6; i++) params.white[i]=analogRead(sensor[i]);  
    SerialPort.println("done");      
  }
  //naar geheugen schrijven
  EEPROM_writeAnything(0, params);
}

void onStop()
{
  params.run = false;
  digitalWrite(AIN1,LOW);
  digitalWrite(AIN2,LOW);
  digitalWrite(BIN1,LOW);
  digitalWrite(BIN2,LOW);

}

void onStart()
{
 params.run = true;
 iTerm = 0;
}

unsigned long last = millis();

void button()
{
  if (millis() - last > 500)
  {
    params.run = !params.run;
    iTerm = 0;
    last = millis();
  }
}

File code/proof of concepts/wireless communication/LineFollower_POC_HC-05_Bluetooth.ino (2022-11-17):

//Bij Arduino Uno Serial. Gebruiken
//Bij Arduino Leonardo Serial1. Gebruiken
//!!!!

int state = 0;

void setup() {
  pinMode(13, OUTPUT);
  digitalWrite(13, LOW);
  Serial1.begin(9600); // Default communication rate of the Bluetooth module
}

void loop() {
  if(Serial1.available() > 0){ // Checks whether data is comming from the serial port
    state = Serial1.read(); // Reads the data from the serial port
 }

 if (state == '0') {
  digitalWrite(13, LOW); // Turn LED OFF
  Serial1.println("LED: OFF"); // Send back, to the phone, the String "LED: ON"
  state = 0;
 }
 else if (state == '1') {
  digitalWrite(13, HIGH);
  Serial1.println("LED: ON");;
  state = 0;
 } 
}
